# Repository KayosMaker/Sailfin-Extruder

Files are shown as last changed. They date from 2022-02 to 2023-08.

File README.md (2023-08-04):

# This fork is no longer maintained.  I leave it for anyone wanting sailfin for voron heatserts or old sharkfin.  [Sharkfin is updated and now has it's own repo.](https://github.com/KayosMaker/Sharkfin_Extruder)
# For Sailfin, visit the home repo.

# Sailfin-Extruder
A lightweight compact extruder with 5:1 gearing using BMG dual drive.   It is capable of pushing up to 48mm^3/s through a 0.4 nozzle.

Footprint is a very compact 41x45mm and weighs 107g (with steel fasteners).

Regular and mirrored version.   STEP files provided.  

There also is a version of the middle body which is compatible with toolheads designed for the Sherpa extruder.

Special thanks to Anlin over at Annex Engineering and his Sherpa mini extruder for inspiring the creation of Sailfin.

Sailfin

Sailfin Scale

# BOM
* [LDO 17mm Nema14 Stepper with gear LDO-36STH17-1004AHG](https://www.printedsolid.com/products/ldo-nema-14-motor-ldo-36sth17-1004ahg?variant=32690500370517) or 20mm version LDO-36STH20-0504AHG which has more torque.
* [Bondtech BMG or clone internals.  Triangle Lab preferred](https://www.aliexpress.com/item/4000021186440.html)
* 1x M3x25 BHCS (SHCS may be used as well for all BHCS)
* 2x M3x14 BHCS
* 2x M3x10 BHCS
* 5x M3 Heatserts [McMaster](https://www.mcmaster.com/94459A130/) [AliExpress M3xD4.6x4](https://www.aliexpress.com/item/4000232858343.html)
* Short length 2mm ID, 4mm OD PTFE tube.
* Optional [Nema14 heatsink](https://www.filastruder.com/products/heatsink-for-pg35l-geared-stepper-motor?_pos=5&_sid=4f2b94743&_ss=r).  Enables higher motor current and more torque.  The motor is same diam as other 540 size RC motors so there are other heatsinks available from RC shops.
* Optional [Thermal tape for the heatsink](https://smile.amazon.com/Thermal-Adhesive-Performance-Heatsink-Computer/dp/B085CLXM7J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)

# ASSEMBLY
Assembly is fairly straightforward.  

There are two parts with small membranes in holes to make printing a solid bridge.  Drill with 3mm drill bit the membrane on the lever and the membrane on the rear piece.

You may need to either push the white gear down 1-2 mm if it rubs on the Nema 14 motor.  Alternatively you may carefully grind off 1-2mm of the shaft.  Be careful of heat so you don't melt the nylon gear.

The cut guide helper is intended to help you cut the PTFE tube.   Place the PTFE tube in your toolhead and position the cut guide above it.  Use a razor blade to cut the tube.  It's helpful to countersink the top end of the tube with a chamfer bit or a conical deburring tool.

# TOOLHEADS

Toolheads are available for the following:
* Tiny-M V3 Gantry Dragon Toolhead
* Tiny-M V4 Gantry Toolhead (on Tiny-M GitHub)
* Voron V0 Dragon
* Voron V0 V6 Screw Mount

There is a version of the middle body that should be compatible with most Sherpa toolheads.  The motor sits a couple mm lower on the Sailfin, so you may also need a 2mm thick printed spacer to raise the Sailfin.

If you design a toolhead around it, let me know and i'll link or post STLs here.

There will be a Sailfin toolhead for CroXY soon.   

[Nice V0 toolhead that supports Sailfin](https://github.com/KurioHonoo/Mini-AfterSherpa/)

# MODS

[Sharkfin now has it's own repo.](https://github.com/KayosMaker/Sharkfin_Extruder)

[Sharkfin](https://github.com/KayosMaker/Sailfin-Extruder/tree/main/Usermods/KayosMaker/Sharkfin)

Sharkfin is a slightly reimagined Sailfin.  These mods were more to satisfy my own neurosis, than actually being strictly necessary.  My goals were as follows: 
* alter the motor location so that a spacer isn't needed to mount the extruder on Mantis
* move the motor enough so that the extruder mounting screw and lower motor mounting screw do not interfere with each other
* lengthen tension arm slightly so it's actually possible to move it with your thumb while its mounted in the tight space on Mantis
* add 3rd screw to front piece, so both the tension arm pivot and the driven gear are supported on both sides
* maintain sailfin motor mounting angle, so pcb mounting brackets made for sailfin work on sharkfin as well

[Sailfin for Voron Heat Inserts](https://github.com/KayosMaker/Sailfin-Extruder/tree/main/Usermods/KayosMaker/Sailfin_for_Voron_heat_inserts)

Sailfin for Voron heat inserts is just that.  It's a very minorly finessed stock Sailfin with holes altered to fit our standard heatsert in Voron land.  I like to debadge things so I also did that while I was at it.  

[PCB Mount](https://github.com/KayosMaker/Sailfin-Extruder/tree/main/Usermods/KayosMaker/Sailfin_PCB_mounts)

Mounting plate for the pancake PCB or Timmit PCB common on v0 and other Printers for Ants.  

[CAN Toolhead Board Mounts](https://github.com/KayosMaker/CANboard_Mounts)

This link leads to a seperate repository.  Included in that repo are mounts for Sailfin that work with the Mellow SHT-36 board, as well as mounts for the BTT EBB-36.  Included are basic no strain relief mounting plates, as well as mounting plates with built in strain relief.

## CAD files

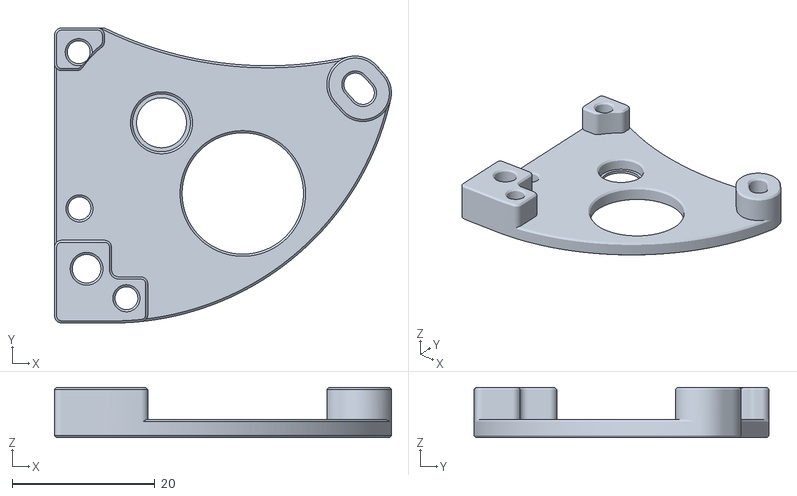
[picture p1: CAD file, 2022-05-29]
STL/Rear.stl
47.2 x 41.4 x 7.07

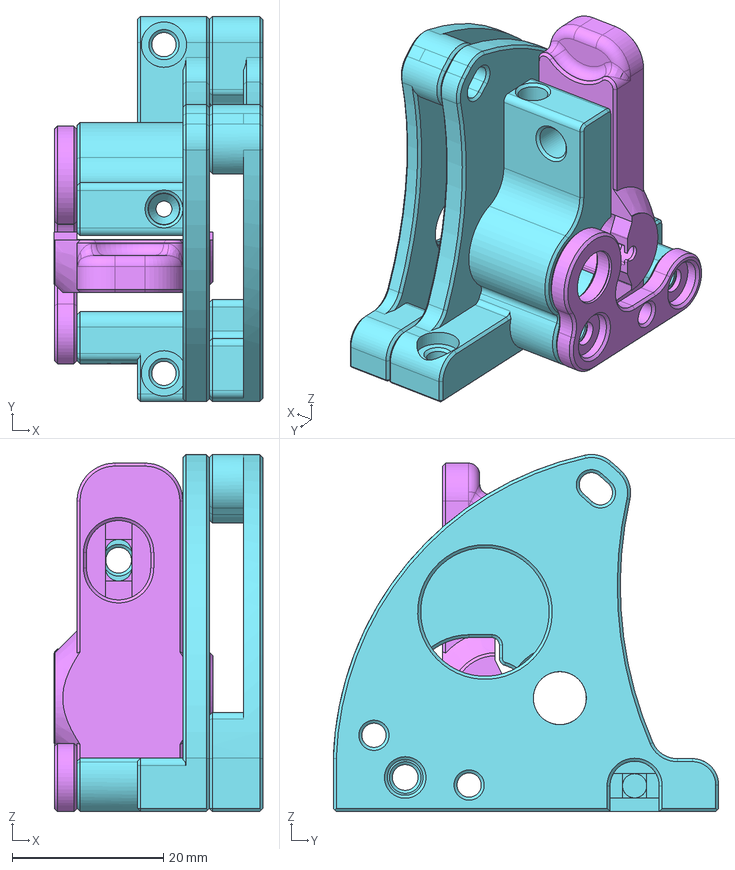
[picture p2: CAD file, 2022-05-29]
Usermods/KayosMaker/Sailfin_for_Voron_heat_inserts/CAD/Sailfin Printed.step
27.6 x 51.0 x 47.2 mm
Rear
Lever
Front
Sherpa Mid

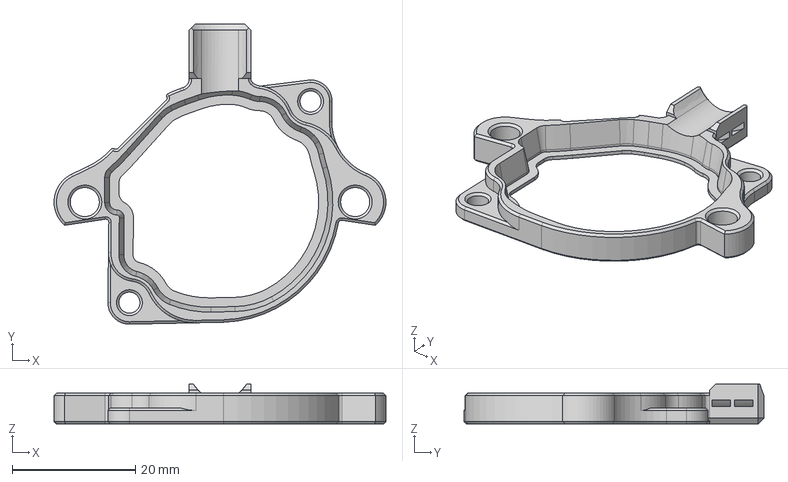
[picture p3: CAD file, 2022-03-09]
Usermods/KayosMaker/Sailfin_PCB_mounts/CAD/universal pcb backer.step
53.8 x 48.7 x 6.48 mm

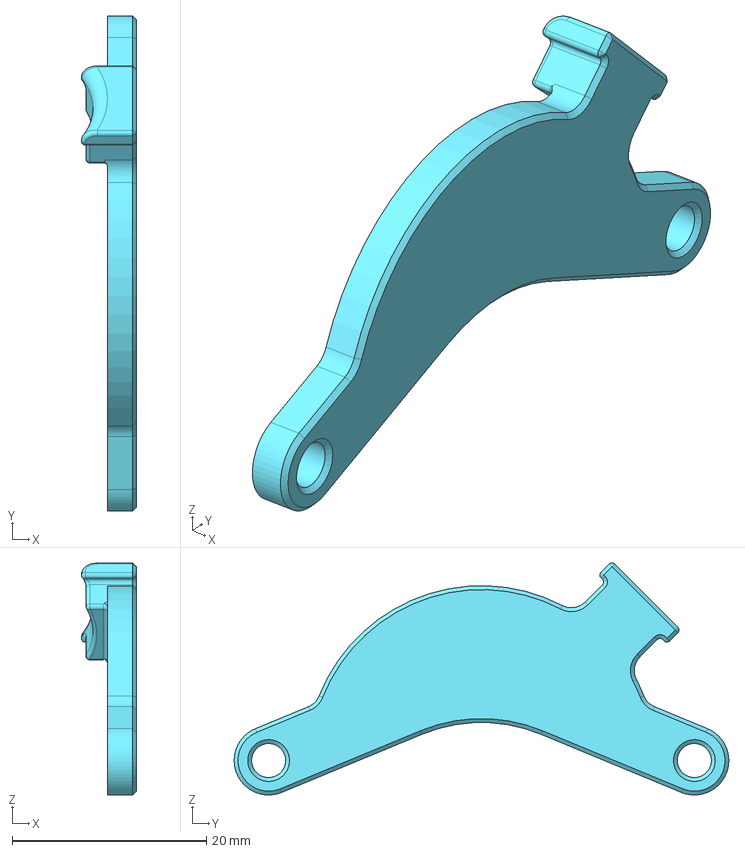
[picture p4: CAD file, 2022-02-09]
Usermods/KayosMaker/Sharkfin/CAD/strain_relief v2.step
5.69 x 50.9 x 23.9 mm

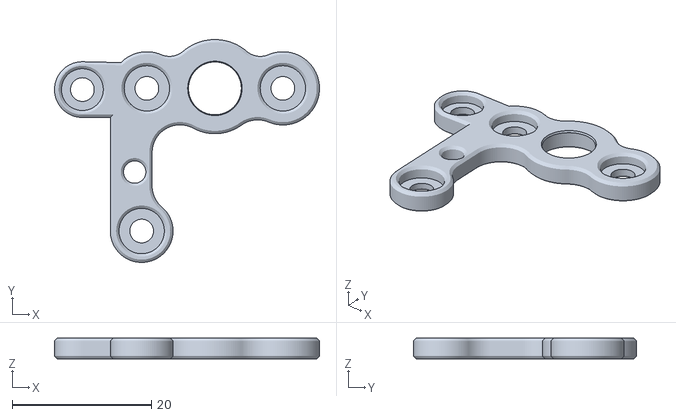
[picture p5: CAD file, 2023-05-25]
Usermods/KayosMaker/Sharkfin/STLs/Front with XOL2 ear v1.stl
38.0 x 32.0 x 3.00

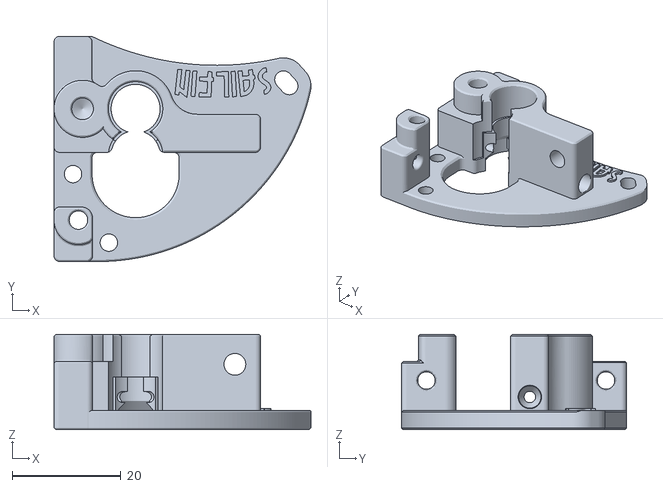
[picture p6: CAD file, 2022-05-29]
STL/Mid.stl
47.2 x 41.4 x 17.5

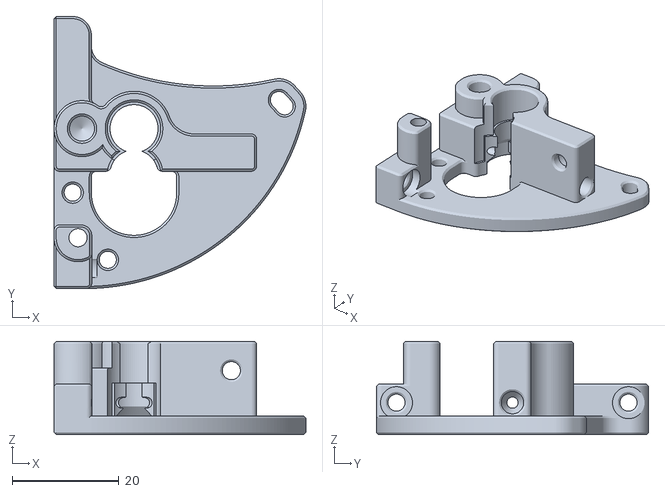
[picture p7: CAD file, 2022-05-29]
Usermods/KayosMaker/Sailfin_for_Voron_heat_inserts/STLs/Sherpa Mid.stl
47.2 x 51.0 x 17.5

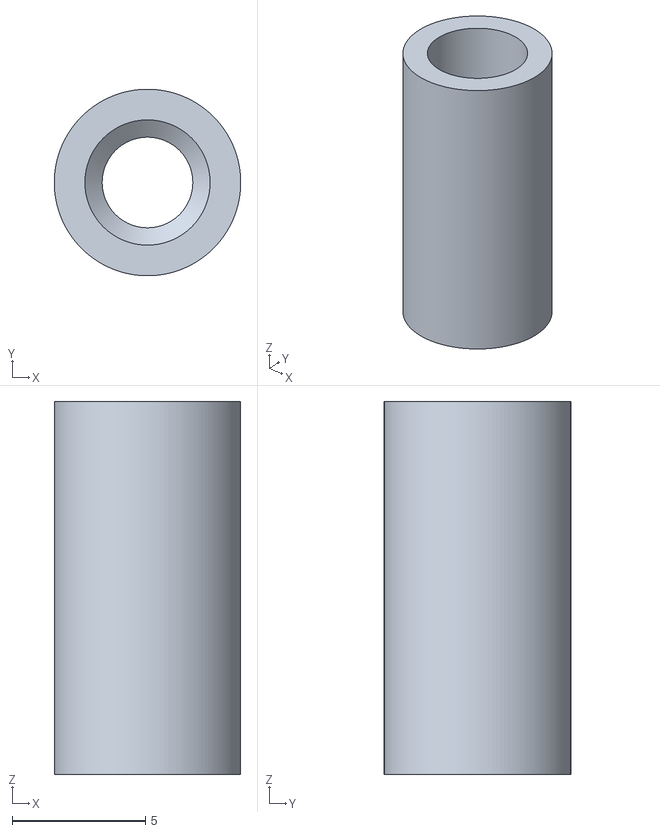
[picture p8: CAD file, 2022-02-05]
Usermods/KayosMaker/Sailfin_PCB_mounts/STLs/14mm spacer forLDO 36mm Pancake Stepper.stl
7.00 x 7.00 x 14.0

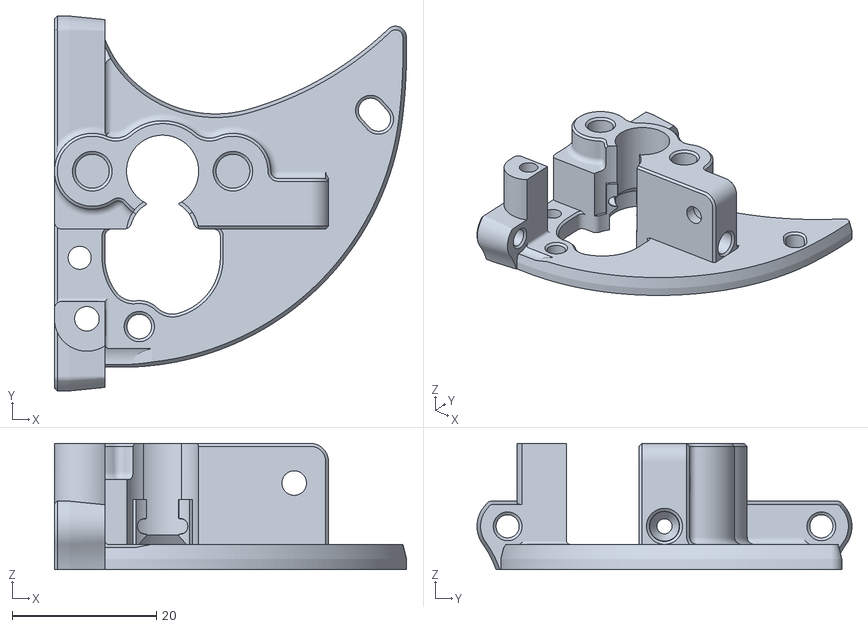
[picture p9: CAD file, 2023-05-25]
Usermods/KayosMaker/Sharkfin/STLs/RIDGA Sherpa Mid.stl
48.8 x 52.0 x 17.5

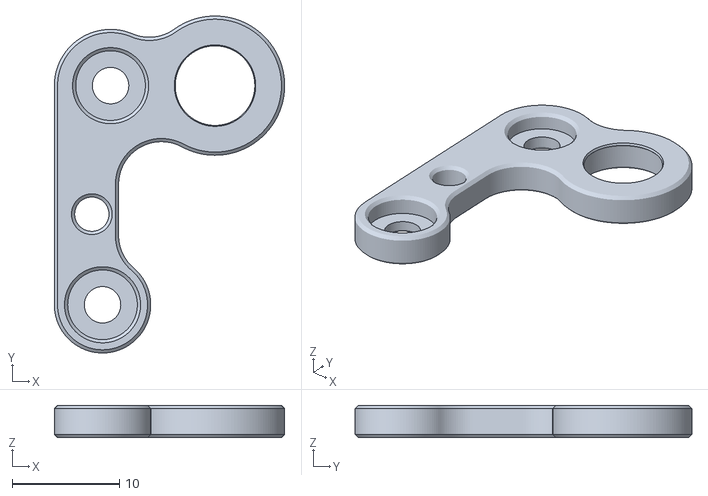
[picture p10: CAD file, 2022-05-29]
STL/Front.stl
21.5 x 31.5 x 3.00

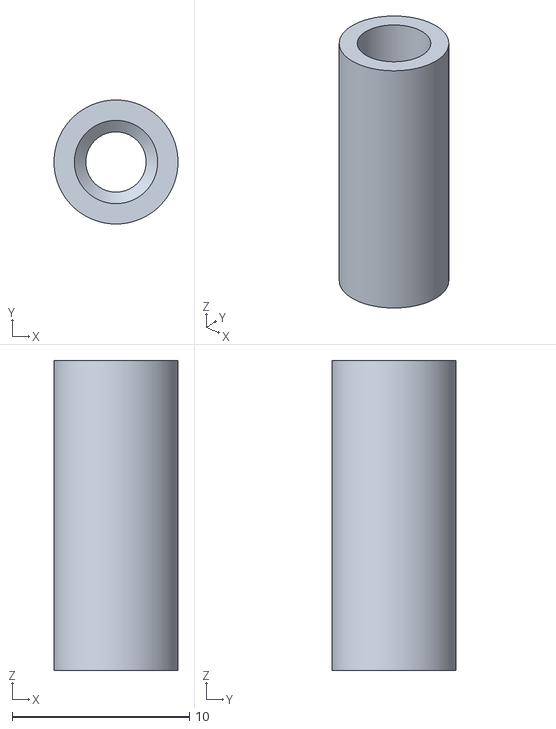
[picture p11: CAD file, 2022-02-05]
Usermods/KayosMaker/Sailfin_PCB_mounts/STLs/spacer for dfh motor.stl
7.00 x 7.00 x 17.5

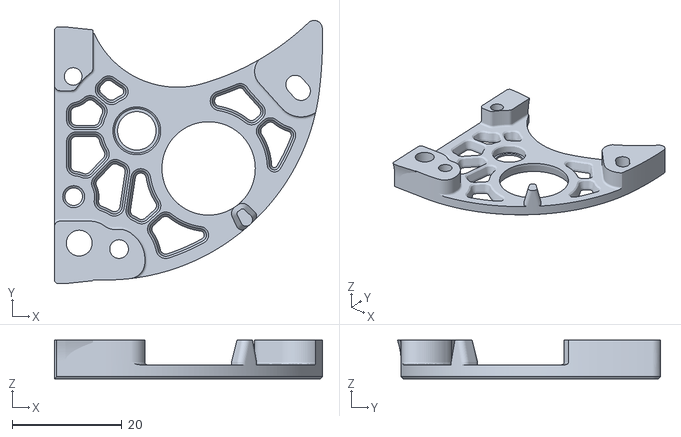
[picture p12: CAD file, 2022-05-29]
Usermods/KayosMaker/Sharkfin/STLs/Rear.stl
48.8 x 48.0 x 7.07

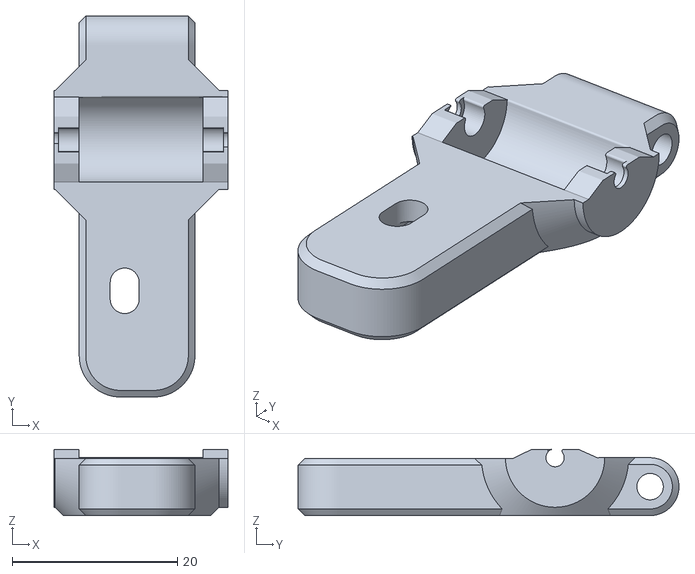
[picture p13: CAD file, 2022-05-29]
STL/Lever.stl
21.0 x 46.1 x 8.00

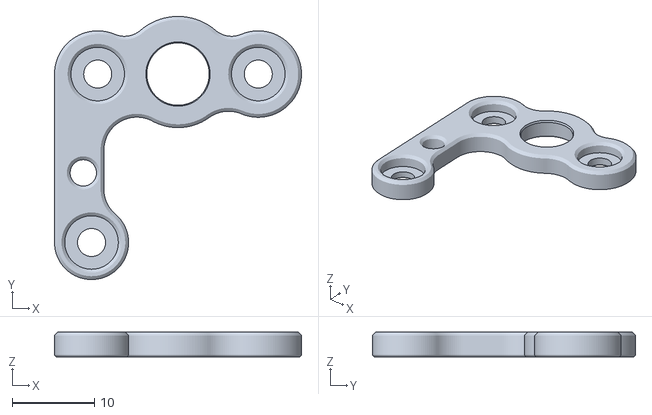
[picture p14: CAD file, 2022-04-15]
Usermods/KayosMaker/Sharkfin/STLs/Front.stl
30.0 x 32.0 x 3.00

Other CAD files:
Usermods/KayosMaker/Sailfin_PCB_mounts/STLs/pcb backer for timmit or pancake board.stl
Usermods/KayosMaker/Sharkfin/STLs/thumb lever.stl
Usermods/KayosMaker/Sharkfin/STLs/Front with ear for Annex K3.stl
Usermods/KayosMaker/Sharkfin/STLs/Sherpa Mid.stl
Usermods/KayosMaker/Sailfin_for_Voron_heat_inserts/STLs/Front.stl
Usermods/KayosMaker/Sailfin_for_Voron_heat_inserts/STLs/Lever.stl
Usermods/KayosMaker/Sailfin_for_Voron_heat_inserts/STLs/Rear.stl
Usermods/KayosMaker/Sharkfin/STLs/v0 style strain relief for sailfin.stl

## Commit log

2022-02-04 add my version
    in usermods
    [Front.stl, Lever.stl, Rear.stl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]
2022-02-04 add missing counterbore for mounting screw
    add fixed cad and stl
    [Sailfin for Voron heatserts v1.step, Sherpa Mid.stl]
2022-02-05 add pcb mount
    [sailfin pancake pcb mount and strain relief.step, sailfin pancake pcb mount and strain relief.stl, spacer for dfh motor.stl]
2022-02-05 Create 14mm spacer forLDO 36mm Pancake Stepper.stl
    [14mm spacer forLDO 36mm Pancake Stepper.stl]
2022-02-08 Create strain relief for sailfin.stl
    [strain relief for sailfin.stl]
2022-02-09 Create strain_relief v2.step
    [strain_relief v2.step]
2022-03-01 fix strain relief interference with 14 pin insertion
    [sailfin pancake pcb mount and strain relief.step, sailfin pancake pcb mount and strain relief.stl]
2022-03-09 update pcb mount to universal type
    add universal pcb mount
    [14mm spacer forLDO 36mm Pancake Stepper.stl, pcb backer for timmit or pancake board.stl, sailfin pancake pcb mount and strain relief.step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]
2022-04-15 add sharkfin stls and cad
    [Front with ear for Annex K3.stl, Front.stl, Lever.stl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]
2022-05-29 add back basic sailfin for voron heatserts
    also fix a hole that was the wrong size on sharkfin
    [Front.stl, Lever.stl, Rear.stl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]
2022-05-29 rename folders
    [14mm spacer forLDO 36mm Pancake Stepper.stl, Front with ear for Annex K3.stl, Front.stl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]
2023-05-18 add RIDGA parts
    [RIDGA Sherpa Mid.stl]
2023-05-25 add ridga and xol2 parts to Sharkfin stls
    [Front with XOL2 ear v1.stl, RIDGA Sherpa Mid.stl]
